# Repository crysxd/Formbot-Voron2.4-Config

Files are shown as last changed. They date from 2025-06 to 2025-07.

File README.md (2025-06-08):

# Formbot Voron 2.4 R2 Pro+

This is a basic config for the Formbot Voron 2.4 R2 Pro+ with instructions as a PDF file. I build the entire machine on stream:

https://www.youtube.com/watch?v=lysE0Ywv53w&list=PL1fjlNqlUKnUwgfOdnnUz_YEgj1KIZx8G&index=12

You can follow the streams and build along, but also keep an eye on the [PDF guide](https://github.com/crysxd/Voron2.4-Config/blob/main/Build%20Guide.pdf) as I e.g. later in the streams found out something could have been done better. It also goes into more detail on flashing the CB1, M8P and SB2209 and contains a list with things you need to print. You can also use my Orca Project files in the STL folder.

If you want to use my config, please compare your wiring to my [PDF guide](https://github.com/crysxd/Voron2.4-Config/blob/main/Build%20Guide.pdf).

If you plan to buy this kit please consider to use my affiliate link so I get a small kick back :) 
https://www.formbot3d.com/products/voron-24-r2-pro-corexy-3d-printer-kit-with-m8p-cb1-board-and-canbus-wiring-system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

The kit as I build it comes with:

- BTT CB1
- BTT M8P 2.0
- BTT SB2209 RP2040
- BTT HDMI5 screen

If a later revision of the kit uses different hardware please afjust accordingly

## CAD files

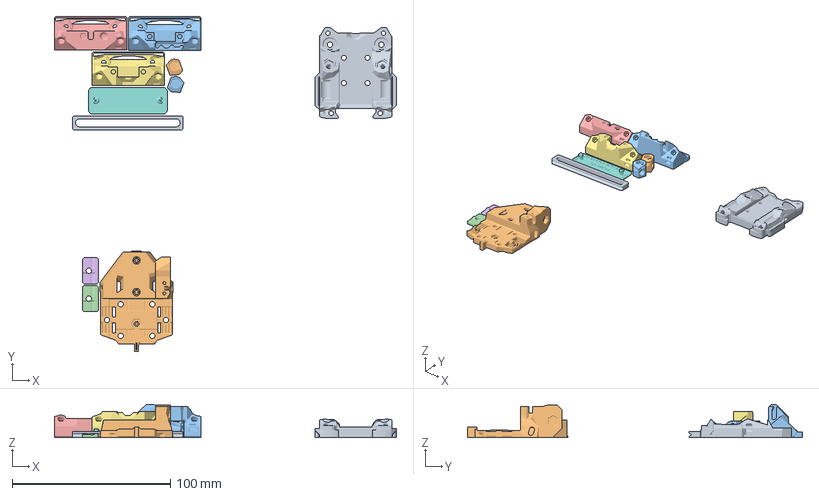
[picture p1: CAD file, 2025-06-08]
STLs/5) Tap.3mf
216.1 x 211.6 x 21.1 mm
Tap_Front_r8.stl
[a]_Tap_Center_r8.stl
Tap_Upper_Wired_r8.stl
[a]_Tap_Belt_Cover_r8_x2.stl x 2
Tap_Upper_D2HW_r8.stl
Tap_Upper_PCB_r8.stl
Printed_Cut_Guide.stl
MGN9_Assembly_Tool.stl
Tap_Center_right_r8.stl
Tap_Center_left_r8.stl

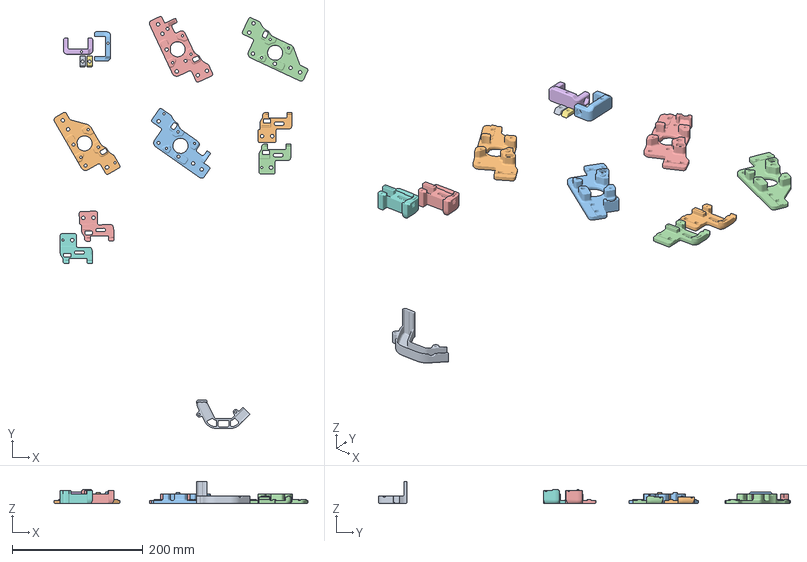
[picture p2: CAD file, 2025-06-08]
STLs/2) AB drives + idlers.3mf
388.8 x 631.0 x 34.0 mm
[a]_cable_cover.stl
front_idler_right_upper.stl
[a]_tensioner_right.stl
front_idler_left_lower.stl
front_idler_left_upper.stl
[a]_tensioner_left.stl
[a]_z_chain_retainer_bracket_x2.stl x 2
front_idler_right_lower.stl
b_drive_frame_lower.stl
a_drive_frame_lower.stl
b_drive_frame_upper.stl
a_drive_frame_upper.stl

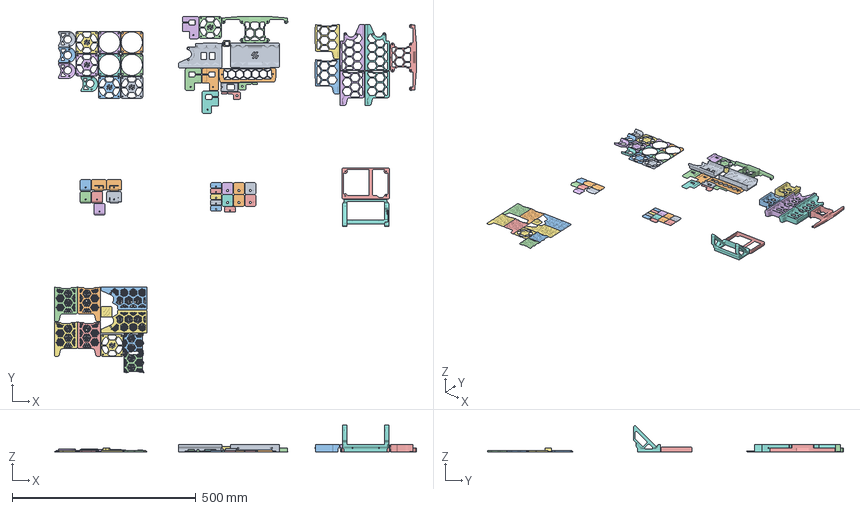
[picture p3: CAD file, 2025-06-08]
STLs/11) Skirts.3mf
983.8 x 968.4 x 72.4 mm
bottom_panel_maghold_panel_x6.stl x 6
[a]_fan_grill_retainer_x2.stl x 4
front-skirt-300-mesh-right.stl
BTT HDMI5 V1_2 mount frame_Regular.stl
front-skirt-300-mesh-left.stl
[a]_fan_grill_b_x2.stl x 3
side-skirt-300-mesh-left.stl
side_fan_support_x2.STL x 2
side-skirt-300-mesh-left(1).stl
[a]_fan_grill_a_x2.stl x 2
BTT HDMI5 V1_2 mount bracket_Regular.stl
[a]_belt_guard_b_x2.stl x 2
side-skirt-300-mesh-right.stl
[a]_belt_guard_a_x2.stl x 2
side-skirt-300-mesh-right(1).stl
rear_center_skirt_300.stl
side-skirt-center-mesh.stl x 2
rear-skirt-logo-insert.stl
keystone_panel.stl
exhaust_filter_grill.stl
bottom_panel_magclip_skirt_x6.stl x 6
[a]_exhaust_fan_grill.stl
z_belt_cover_b_x2.stl x 2
front_skirt_a_300.stl
z_belt_cover_a_x2.stl x 2
front_skirt_b_300.stl
side_skirt_a_300_x2.stl x 2
bowden_retainer.stl
bottom_panel_hinge_x2.stl x 3
[a]_exhaust_filter_mount_x2.stl x 2
side_skirt_b_300_x2.stl x 2
[a]_keystone_blank_insert.stl
bottom_panel_clip_x4.stl x 4

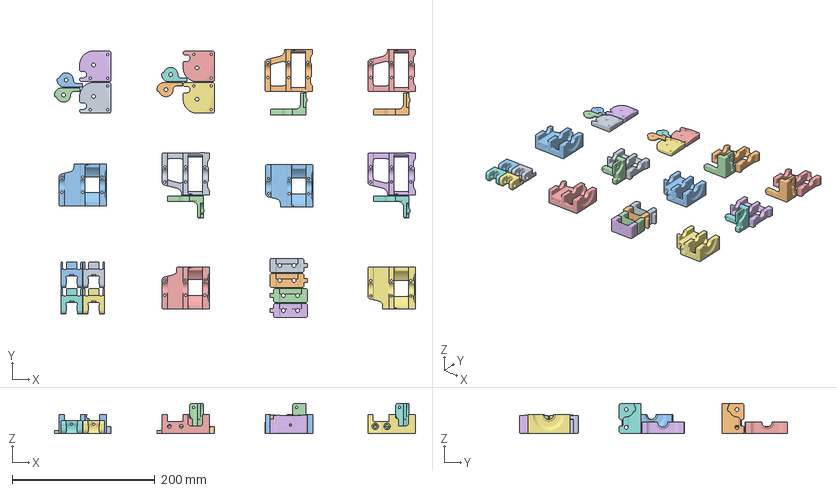
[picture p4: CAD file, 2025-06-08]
STLs/1) Z Drive.3mf
504.9 x 375.3 x 42.0 mm
z_tensioner_bracket_b_x2.stl x 2
z_drive_retainer_b_x2.stl x 2
z_drive_main_b_x2.stl x 2
z_motor_mount_b_x2.stl x 2
z_drive_main_a_x2.stl x 2
z_drive_retainer_a_x2.stl x 2
z_motor_mount_a_x2.stl x 2
[a]_z_tensioner_9mm_x4.stl x 4
z_tensioner_bracket_a_x2.stl x 2
[a]_z_drive_baseplate_a_x2.stl x 2
[a]_z_drive_baseplate_b_x2.stl x 2
[a]_belt_tensioner_b_x2.stl x 2
[a]_belt_tensioner_a_x2.stl x 2

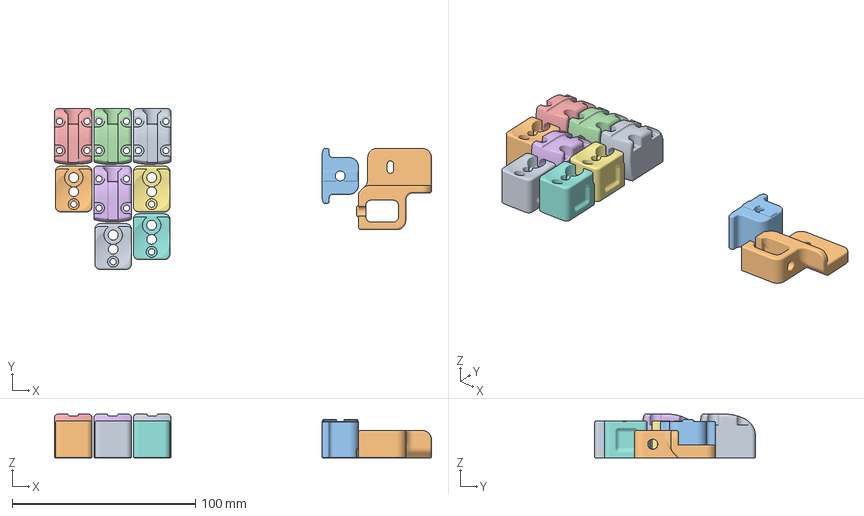
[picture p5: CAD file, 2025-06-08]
STLs/4) Z Axis.3mf
205.6 x 87.8 x 24.0 mm
z_joint_lower_x4.stl x 4
z_chain_bottom_anchor.stl
z_chain_guide.stl
z_joint_upper_x4.stl x 4

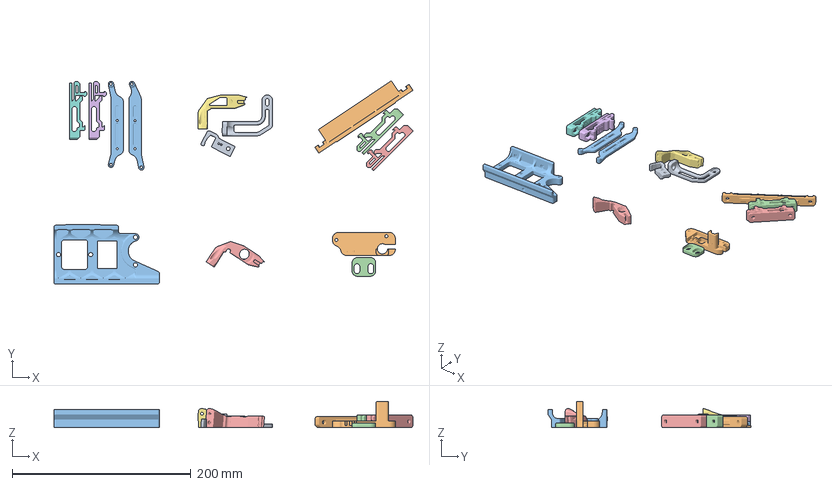
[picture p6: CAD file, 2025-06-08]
STLs/8) Electronics.3mf
402.0 x 227.7 x 29.3 mm
PSU_stabilizer_50mm.stl
Umbilical_cable_PG7_5mm_cable_cutout.stl
Manta_M8P_2pc.stl
Y bumper.stl
cw2-cable-bridge-pg7-can.stl
lrs_200_psu_bracket_x2.stl x 4
CW2 Cable_bridge.stl
Printed_Part_for_CAN_Cable_V1.2.stl
wago_221-415_mount_3by5.stl
power_inlet_filtered.stl

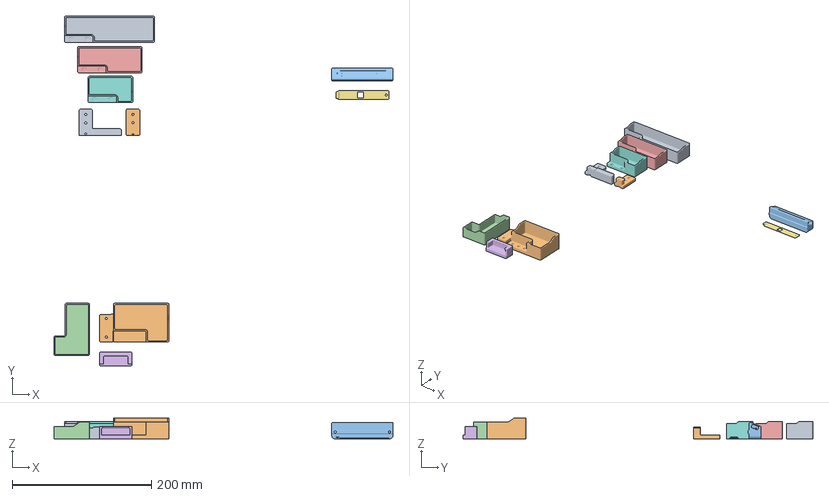
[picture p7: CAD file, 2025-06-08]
STLs/12) Addons.3mf
486.6 x 502.3 x 30.0 mm
0-SOLID-1
bucket-6x3-magnets.stl
happycam_main300.stl
bucket-insert.stl
0-SOLID-2
brush-holder-6x3-magnets.stl
cameradoor_120.stl
0-SOLID-3
0-SOLID-4
0-SOLID-5

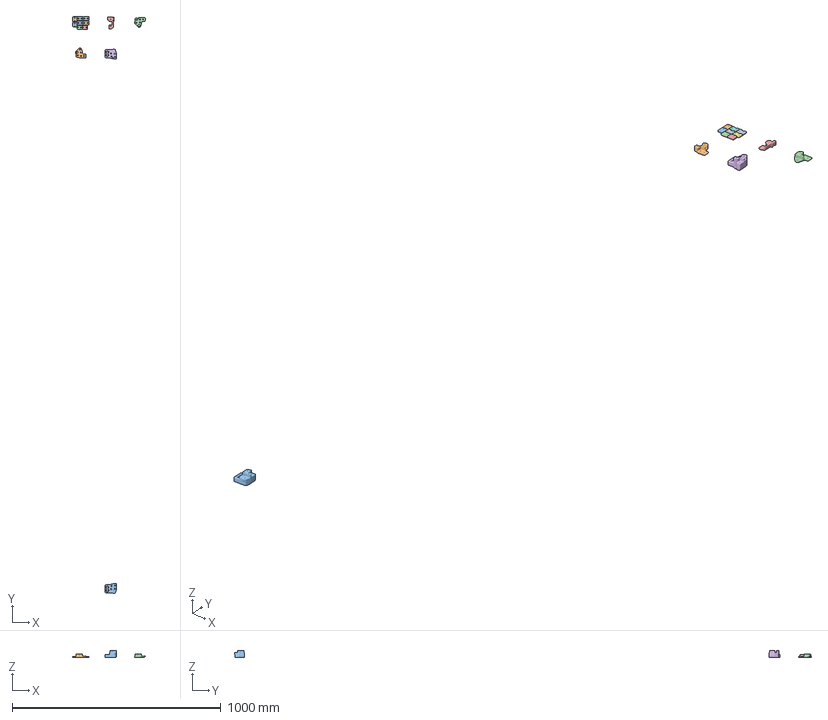
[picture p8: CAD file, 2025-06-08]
STLs/3) Gantry.3mf
348.0 x 2766.5 x 34.0 mm
[a]_z_belt_clip_upper_x4.stl x 4
xy_joint_left_upper_MGN12.stl
xy_joint_left_lower_MGN12.stl
xy_joint_right_upper_MGN12.stl
[a]_endstop_pod_D2F_switch.stl
xy_joint_right_lower_MGN12.stl
[a]_z_belt_clip_lower_x4.stl x 4

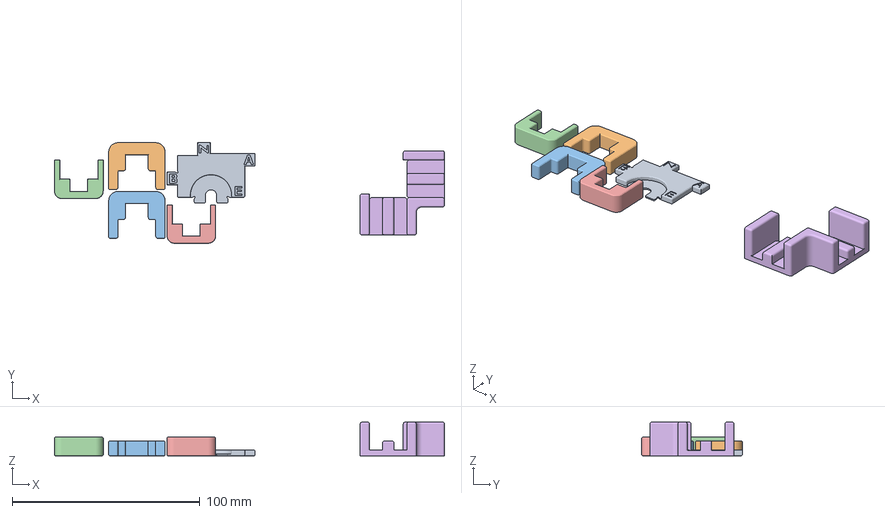
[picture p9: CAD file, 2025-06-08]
STLs/6) Tools.3mf
208.0 x 53.7 x 18.0 mm
pulley_jig.stl
MGN12_rail_guide_x2.stl x 2
MGN9_rail_guide_x2.stl x 2
jig.step

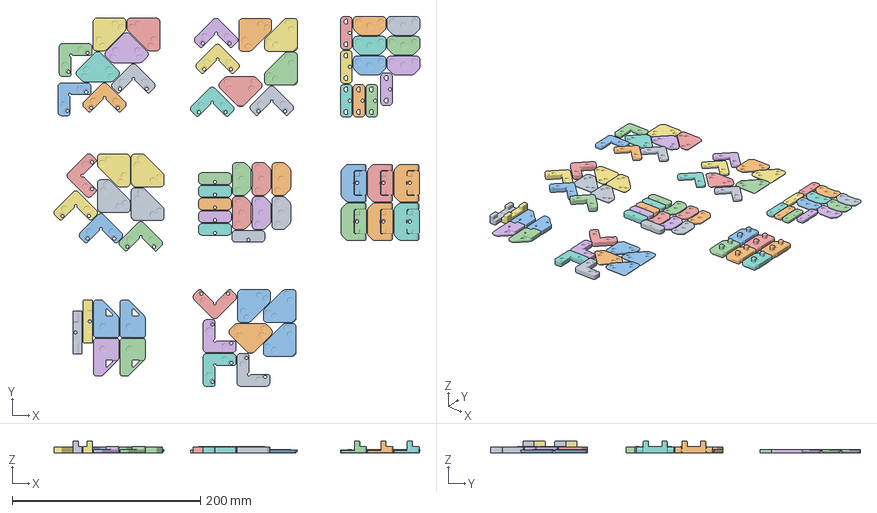
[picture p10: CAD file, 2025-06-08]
STLs/10) Panels.3mf
388.7 x 393.0 x 13.0 mm
magnetic_midspan_panel_clip_cap_3mm.stl x 12
magnetic_corner_panel_clip_cap.stl x 16
magnetic_midspan_panel_clip_base_3mm.stl x 6
midspan_6mm.stl x 6
corner_6mm.stl x 8
handle_a_x2.stl x 2
magnetic_corner_panel_clip_base_3mm.stl x 8
door_hinge_x6.stl x 6
handle_b_x2.stl x 2
latch_x2.stl x 2

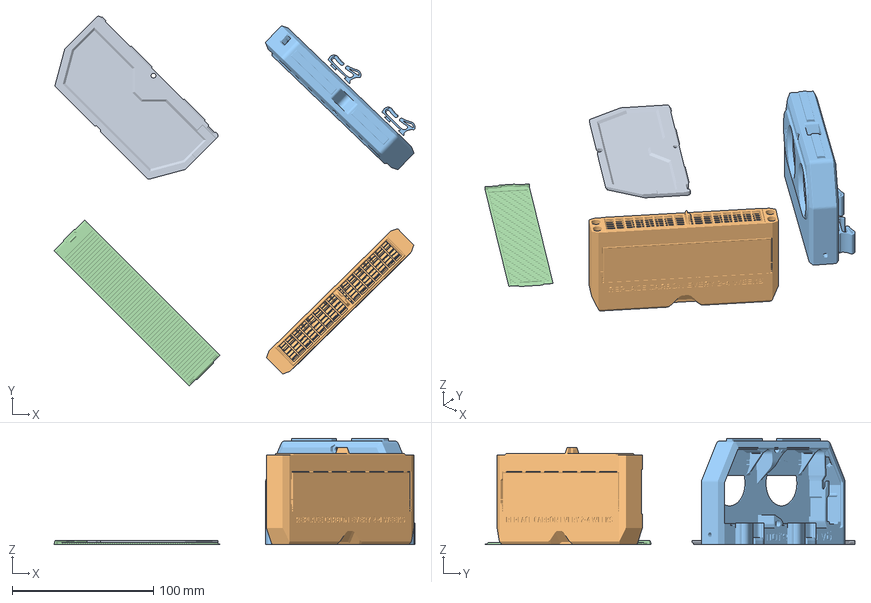
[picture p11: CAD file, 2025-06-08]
STLs/7) Nevermore.3mf
255.2 x 261.3 x 75.2 mm
V6_Plenum_Lid.stl
v6_Cartridge_90deg.stl
V6_Plenum[2020_extrusion].stl
[a]V6_Jalousie_Slicer.stl

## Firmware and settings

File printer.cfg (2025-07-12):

[include mainsail.cfg]
[include macros.cfg]





##########################################################################################################################################
##########################################################################################################################################
##########################################################################################################################################
# 	Basic config, need to check!
##########################################################################################################################################
##########################################################################################################################################
##########################################################################################################################################


# M8P 
[mcu]
canbus_uuid: f8bbc90dfa2d #CANBUS ID FOR M8P here replace with yours

# SB2209
[mcu ebb]
canbus_uuid: ef0499b67b66 #CANBUS ID FOR SB2209 here, replace with yours

[stepper_x]
# ADJUST 250 buid
# position_endstop: 250
# position_max: 250

# 300 build
position_endstop: 300
position_max: 300 

# ADJUST 350 buid
# position_endstop: 350
# position_max: 350

[stepper_y]
# ADJUST 250 buid
# position_endstop: 253
# position_max: 253

# 300 build
position_endstop: 303
position_max: 303 

# ADJUST 350 buid
# position_endstop: 353
# position_max: 353

[stepper_z]
# ADJUST 250 buid
# position_max: 240

# 300 build
position_max: 290

# ADJUST 350 buid
# position_max: 340

[extruder]
max_temp: 250 # ADJUST for Dragon hotend: 285

[quad_gantry_level]
# ADJUST: 250 build
# gantry_corners:
#	-60,-10
#	310, 320
# points:
#	25,25
#	25,200
#	225,200
#	225,25

# 300 build
gantry_corners:
	-60,-10
	360,370
points:
	25,25
	25,250
	275,250
	275,25

# ADJUST: 350 build
# gantry_corners:
# 	-60,-10
# 	410,420
# points:
# 	25,25
# 	25,300
# 	325,300
# 	325,25

[safe_z_home]
# ADJUST: 250 build
# home_xy_position: 125,125

# 300 build
home_xy_position: 150, 150

# ADJUST: 350 build
# home_xy_position: 175,175

[bed_mesh]
# ADJUST: 250 build
#mesh_max: 240,240

# 300 build
mesh_max: 290,290

# ADJUST: 350 build
#mesh_max: 340,340

[resonance_tester]
# ADJUST: 250 build
# probe_points: 125, 125, 20

# 300 build
probe_points: 150, 150, 20

# ADJUST: 350 build
# probe_points: 175, 175, 20



#####################################################################
# 	TMC autotune for silent and strong steppers
#####################################################################

# Uncomment below after installing the TMC autotune plugin
# This is optional but recommended
# https://github.com/andrewmcgr/klipper_tmc_autotune

# [autotune_tmc extruder]
# motor: moons-cse14hra1l410a
#
# [autotune_tmc stepper_x]
# motor: moons-ms17hd6p420I-05
#
# [autotune_tmc stepper_y]
# motor: moons-ms17hd6p420I-05
#
# [autotune_tmc stepper_z]
# motor: moons-ms17hd6p420I-05
#
# [autotune_tmc stepper_z1]
# motor: moons-ms17hd6p420I-05
#
# [autotune_tmc stepper_z2]
# motor: moons-ms17hd6p420I-05
#
# [autotune_tmc stepper_z3]
# motor: moons-ms17hd6p420I-05







##########################################################################################################################################
##########################################################################################################################################
##########################################################################################################################################
# 	Advanced config, not needed to edit for basic build
##########################################################################################################################################
##########################################################################################################################################
##########################################################################################################################################




#####################################################################
# 	MISC
#####################################################################


[printer]
kinematics: corexy
max_velocity: 700  
max_accel: 12000
max_z_velocity: 25
max_z_accel: 250
square_corner_velocity: 5.0

[idle_timeout]
timeout: 1800

[exclude_object]

[force_move] 
enable_force_move: true

[safe_z_home]
speed: 600
z_hop: 10

[bed_mesh]
speed: 350
horizontal_move_z: 2
mesh_min: 10,10
probe_count: 7,7
adaptive_margin: 5
mesh_pps: 2, 3
algorithm: bicubic
bicubic_tension: 0.2

[temperature_sensor MCU]
sensor_type: temperature_mcu

[temperature_sensor SoC]
sensor_type: temperature_host

[temperature_sensor EBB_NTC]
sensor_type: Generic 3950
sensor_pin: ebb:gpio28

[quad_gantry_level]
speed: 350
horizontal_move_z: 5
retries: 5
retry_tolerance: 0.0075
max_adjust: 10

[probe]
pin: ^ebb:gpio22
x_offset: 0
y_offset: 0
#z_offset: -1.900
lift_speed: 30
activate_gcode:
    {% set PROBE_TEMP = 150 %}
    {% set MAX_TEMP = PROBE_TEMP + 5 %}
    {% set ACTUAL_TEMP = printer.extruder.temperature %}
    {% set TARGET_TEMP = printer.extruder.target %}

    {% if TARGET_TEMP > PROBE_TEMP %}
        { action_respond_info('Extruder temperature target of %.1fC is too high, lowering to %.1fC' % (TARGET_TEMP, PROBE_TEMP)) }
        M109 S{ PROBE_TEMP }
    {% else %}
        # Temperature target is already low enough, but nozzle may still be too hot.
        {% if ACTUAL_TEMP > MAX_TEMP %}
            { action_respond_info('Extruder temperature %.1fC is still too high, waiting until below %.1fC' % (ACTUAL_TEMP, MAX_TEMP)) }
            TEMPERATURE_WAIT SENSOR=extruder MAXIMUM={ MAX_TEMP }
        {% endif %}
    {% endif %}

#####################################################################
# 	X/Y Stepper Settings
#####################################################################

## X Stepper on Motor1(B Motor)
[stepper_x]
step_pin: PG9
dir_pin: PD7
enable_pin: !PG11
microsteps: 16
rotation_distance: 40
full_steps_per_rotation:200  
endstop_pin: ^ebb:gpio24
position_min: 0
homing_speed: 100                 
homing_retract_dist: 5
homing_positive_dir: true

[tmc2209 stepper_x]
uart_pin: PG10
interpolate: True
run_current: 0.8
sense_resistor: 0.110
stealthchop_threshold: 0

[stepper_y]
step_pin: PG13
dir_pin: PG12
enable_pin: !PG15
microsteps: 16
rotation_distance: 40
endstop_pin: ^PF3
full_steps_per_rotation:200 
position_min: 0
homing_speed: 100
homing_retract_dist: 5
homing_positive_dir: true

[tmc2209 stepper_y]
uart_pin: PG14
interpolate: True
run_current: 0.8
sense_resistor: 0.110
stealthchop_threshold: 0


#####################################################################
# 	Z Stepper Settings
#####################################################################

## Z0 Stepper - Check wiring diagaram in PDF guide on GitHub!
[stepper_z]
step_pin: PE6
dir_pin: PE5
enable_pin: !PC14
rotation_distance: 40
gear_ratio: 80:16
microsteps: 16
endstop_pin: probe:z_virtual_endstop
position_min: -10
homing_speed: 8
second_homing_speed: 3
homing_retract_dist: 3

[tmc2209 stepper_z]
uart_pin: PC13
interpolate: true
run_current: 0.8
sense_resistor: 0.110
stealthchop_threshold: 1

##	Z1 Stepper - Check wiring diagaram in PDF guide on GitHub!
[stepper_z1]
step_pin: PE2
dir_pin: !PE1
enable_pin: !PE4
rotation_distance: 40
gear_ratio: 80:16
microsteps: 16

[tmc2209 stepper_z1]
uart_pin: PE3
interpolate: true
run_current: 0.8
sense_resistor: 0.110
stealthchop_threshold: 1

##	Z2 Stepper - Check wiring diagaram in PDF guide on GitHub!
[stepper_z2]
step_pin: PB8
dir_pin: PB7
enable_pin: !PE0
rotation_distance: 40
gear_ratio: 80:16
microsteps: 16

[tmc2209 stepper_z2]
uart_pin: PB9
interpolate: true
run_current: 0.8
sense_resistor: 0.110
stealthchop_threshold: 1

##	Z3 Stepper - Check wiring diagaram in PDF guide on GitHub!
[stepper_z3]
step_pin: PB4
dir_pin: !PB3
enable_pin: !PB6
rotation_distance: 40
gear_ratio: 80:16
microsteps: 16

[tmc2209 stepper_z3]
uart_pin: PB5
interpolate: true
run_current: 0.8
sense_resistor: 0.110
stealthchop_threshold: 1


#####################################################################
# 	Bed Heater
#####################################################################

[heater_bed]
heater_pin: PA1
sensor_type: Generic 3950
sensor_pin: PB1
max_power: 1.0
min_temp: 0
max_temp: 120
control: pid
pid_kp: 58.437
pid_ki: 2.347
pid_kd: 363.769


#####################################################################
# 	Fan Control
#####################################################################

[fan_generic nevermore]
##	Print Cooling Fan - CNC_FAN0
pin: PF8
kick_start_time: 0.5
##	Depending on your fan, you may need to increase this value
##	if your fan will not start. Can change cycle_time (increase)
##	if your fan is not able to slow down effectively
off_below: 0.10
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

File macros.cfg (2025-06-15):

[delayed_gcode after_startup_1]
initial_duration: 1.
gcode:
  LIGHT_PENDING
  
[delayed_gcode after_startup_2]
initial_duration: 5.
gcode:
  LIGHT_OFF

[gcode_macro G32]
gcode:
    BED_MESH_CLEAR
    G28
    QUAD_GANTRY_LEVEL
    G28

[gcode_macro FILTER_ON]
gcode:
    SET_FAN_SPEED FAN=nevermore SPEED=0.8

[gcode_macro FILTER_OFF]
gcode:
    SET_FAN_SPEED FAN=nevermore SPEED=0
   
[gcode_macro PRINT_START]
gcode:
    {% set BED_TEMP = params.BED_TEMP|default(60)|float %}
    {% set EXTRUDER_TEMP = params.EXTRUDER_TEMP|default(190)|float %}
    {% set BRUSH_NOZZLE = params.BRUSH_NOZZLE|default(0)|float %}
    LIGHT_PENDING
  	# Start TLM Start G-Code
	# Clear Display
	M117
	# Clear Existing Feedrate
	M220 S100
	# Clear Existing Flowrate
	M221 S100
    # Heat bed
    M140 S{BED_TEMP}
    # Brush nozzle if enabled by param
    {% if BRUSH_NOZZLE > 0 %}
	    G28
        NOZZLE_PRIME_AND_BRUSH EXTRUDER_TEMP={EXTRUDER_TEMP}
    {% endif %}
    G32
    # Wait for Bed
    M190 S{BED_TEMP}
    BED_MESH_CALIBRATE ADAPTIVE=1
	# Move to side and wait for final temps
    M109 S{EXTRUDER_TEMP}
    G1 X1 Y10 Z5 F3000
    G91
    G1 E25 F3600
    
	# Relative Extruder
	M83
	# Set units to millimeters
	G21 
	# Use absolute coordinates
	G90
	# Use absolute distances for extrusion
	M82
	# Fan Off
	M107
    {% if BED_TEMP > 90 %}
      FILTER_ON
    {% endif %}
    
	NOZZLE_PURGE
    LIGHT_PRINTING
    
   

[gcode_macro PRINT_END]
#   Use PRINT_END for the slicer ending script - please customise for your slicer of choice
gcode:
    SAVE_GCODE_STATE NAME=STATE_PRINT_END

    M400                           ; wait for buffer to clear
    G92 E0                         ; zero the extruder
    G1 E-25.0 F3600                ; retract filament

    G91                            ; relative positioning
    G0 Z1.00 X20.0 Y20.0 F20000    ; move nozzle to remove stringing
    TURN_OFF_HEATERS
    M107                           ; turn off fan
    G1 Z2 F3000                    ; move nozzle up 2mm
    G90                            ; absolute positioning
    G0  X125 Y250 F3600            ; park nozzle at rear
    BED_MESH_CLEAR

    GET_POSITION
    
    # The purpose of the SAVE_GCODE_STATE/RESTORE_GCODE_STATE
    # command pair is to restore the printer's coordinate system
    # and speed settings since the commands above change them.
    # However, to prevent any accidental, unintentional toolhead
    # moves when restoring the state, explicitly set MOVE=0.
    RESTORE_GCODE_STATE NAME=STATE_PRINT_END MOVE=0
    LIGHT_OFF
    FILTER_OFF

[gcode_macro LIGHT_PENDING]
gcode:
  SET_LED LED=toolhead_light RED=1 GREEN=0.02 BLUE=0.02 WHITE=0 INDEX=1 TRANSMIT=0
  SET_LED LED=toolhead_light RED=0 GREEN=0 BLUE=0 WHITE=0 INDEX=2 TRANSMIT=0
  SET_LED LED=toolhead_light RED=0 GREEN=0 BLUE=0 WHITE=0 INDEX=3 TRANSMIT=1
  SET_PIN PIN=caselight VALUE=0

[gcode_macro LIGHT_PRINTING]
gcode:
  SET_LED LED=toolhead_light RED=0 GREEN=0.0 BLUE=0.0 WHITE=0.5
  SET_PIN PIN=caselight VALUE=0.8

[gcode_macro LIGHT_OFF]
gcode:
  SET_LED LED=toolhead_light RED=0 GREEN=0.02 BLUE=0 WHITE=0 INDEX=1 TRANSMIT=0
  SET_LED LED=toolhead_light RED=0 GREEN=0 BLUE=0 WHITE=0 INDEX=2 TRANSMIT=0
  SET_LED LED=toolhead_light RED=0 GREEN=0 BLUE=0 WHITE=0 INDEX=3 TRANSMIT=1
  SET_PIN PIN=caselight VALUE=0

[gcode_macro NOZZLE_PRIME_AND_BRUSH]
gcode:
   {% set EXTRUDER_TEMP = params.EXTRUDER_TEMP|default(190)|float %}

  # Move over bucker
  G0 X298 Y303 Z10 F9000

  # Purge
  M104 S{EXTRUDER_TEMP}
  TEMPERATURE_WAIT sensor=extruder MINIMUM={EXTRUDER_TEMP-5} MAXIMUM={EXTRUDER_TEMP+5}
  M83  
  G1 E50 F500
  G1 E-5  F500
  M104 S150

  # Brush
  {% for i in range(10) %}
    G0 X238 Y299 F5000
    G0 X278 Y302 F5000
  {% endfor %}

  G0 Y290 F3000

[gcode_macro NOZZLE_PURGE]
description: Draw a purge line at the front left edge of the build plate
gcode:
  CHOME
  G0 X2.5 Y2 F6000 ; Go to front
  G0 Z0.2 ; Drop to bed
  M83 ; Set extruder to relative mode
  G1 X25 E10 F500 ; Extrude 25mm of filament in a 4cm line
  G1 X50 F5000 ; Quickly wipe away from the filament line
  G1 X75 E2.00 F1500
  G1 E-0.1 F400 ; Retract a little
  G1 Z0.5 ; Raise and begin printing.

[gcode_macro CHOME]
description: Homes XYZ axis only if printer is in a non-homed state
gcode:
  {% if "xyz" not in printer.toolhead.homed_axes or printer["quad_gantry_level"].applied == false %}
    G32
  {% endif %}

[gcode_macro TEST_SPEED]
# Home, get position, throw around toolhead, home again.
# If MCU stepper positions (first line in GET_POSITION) are greater than a full step different (your number of microsteps), then skipping occured.
# We only measure to a full step to accomodate for endstop variance.
# Example: TEST_SPEED SPEED=300 ACCEL=5000 ITERATIONS=10

description: Test for max speed and acceleration parameters for the printer. Procedure: Home -> ReadPositionFromMCU -> MovesToolhead@Vel&Accel -> Home -> ReadPositionfromMCU

gcode:
    # Speed
    {% set speed  = params.SPEED|default(printer.configfile.settings.printer.max_velocity)|int %}
    # Iterations
    {% set iterations = params.ITERATIONS|default(5)|int %}
    # Acceleration
    {% set accel  = params.ACCEL|default(printer.configfile.settings.printer.max_accel)|int %}
    # Minimum Cruise Ratio
    {% set min_cruise_ratio = params.MIN_CRUISE_RATIO|default(0.5)|float %}
    # Bounding inset for large pattern (helps prevent slamming the toolhead into the sides after small skips, and helps to account for machines with imperfectly set dimensions)
    {% set bound = params.BOUND|default(20)|int %}
    # Size for small pattern box
    {% set smallpatternsize = SMALLPATTERNSIZE|default(20)|int %}
    
    # Large pattern
        # Max positions, inset by BOUND
        {% set x_min = printer.toolhead.axis_minimum.x %}
        {% if x_min < 0 %}
            {% set x_min = 0 %}
        {% endif %}
    
        {% set y_min = printer.toolhead.axis_minimum.y %}
        {% if y_min < 0 %}
            {% set y_min = 0 %}
        {% endif %}
    
        {% set x_min = x_min + bound %}
        {% set x_max = printer.toolhead.axis_maximum.x - bound %}
        {% set y_min = y_min + bound %}
        {% set y_max = printer.toolhead.axis_maximum.y - bound %}
    
    # Small pattern at center
        # Find X/Y center point
        {% set x_center = (printer.toolhead.axis_minimum.x|float + printer.toolhead.axis_maximum.x|float ) / 2 %}
        {% set y_center = (printer.toolhead.axis_minimum.y|float + printer.toolhead.axis_maximum.y|float ) / 2 %}
        
        # Set small pattern box around center point
        {% set x_center_min = x_center - (smallpatternsize/2) %}
        {% set x_center_max = x_center + (smallpatternsize/2) %}
        {% set y_center_min = y_center - (smallpatternsize/2) %}
        {% set y_center_max = y_center + (smallpatternsize/2) %}

    # Save current gcode state (absolute/relative, etc)
    SAVE_GCODE_STATE NAME=TEST_SPEED
    
    # Output parameters to g-code terminal
    { action_respond_info("TEST_SPEED: starting %d iterations at speed %d, accel %d" % (iterations, speed, accel)) }
    
    # Home and get position for comparison later:
        M400 # Finish moves - https://github.com/AndrewEllis93/Print-Tuning-Guide/issues/66
        G28
        # QGL if not already QGLd (only if QGL section exists in config)
        {% if printer.configfile.settings.quad_gantry_level %}
            {% if printer.quad_gantry_level.applied == False %}
                QUAD_GANTRY_LEVEL
                G28 Z
            {% endif %}
        {% endif %} 
        # Move 50mm away from max position and home again (to help with hall effect endstop accuracy - https://github.com/AndrewEllis93/Print-Tuning-Guide/issues/24)
        G90
        G1 X{printer.toolhead.axis_maximum.x-50} Y{printer.toolhead.axis_maximum.y-50} F{30*60}
        M400 # Finish moves - https://github.com/AndrewEllis93/Print-Tuning-Guide/issues/66
        G28 X Y
        G0 X{printer.toolhead.axis_maximum.x-1} Y{printer.toolhead.axis_maximum.y-1} F{30*60}
        G4 P1000 
        GET_POSITION

    # Go to starting position
    G0 X{x_min} Y{y_min} Z{bound + 10} F{speed*60}

    # Set new limits
    {% if printer.configfile.settings.printer.minimum_cruise_ratio is defined %}
        SET_VELOCITY_LIMIT VELOCITY={speed} ACCEL={accel} MINIMUM_CRUISE_RATIO={min_cruise_ratio}
    {% else %}
        SET_VELOCITY_LIMIT VELOCITY={speed} ACCEL={accel} ACCEL_TO_DECEL={accel / 2}
    {% endif %}
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

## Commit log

2025-05-20 Udpate config
    [macros.cfg, printer-board-cb1.cfg, printer-board-ebb.cfg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]
2025-06-08 Add README and files
    [1) Z Drive.3mf, 10) Panels.3mf, 11) Skirts.3mf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]
2025-06-08 Update for dragon
    [printer.cfg]
2025-06-08 Remove unused files
    [mainsail.cfg, timelapse.cfg]
2025-06-08 Add missing 350 config
    [printer.cfg]
2025-06-15 Reduce default max temp
    [printer.cfg]
2025-06-15 Move to single file
    [printer-board-ebb.cfg, printer-board-m8p.cfg, printer-extras.cfg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]
2025-06-15 Fix Y endstop
    [printer.cfg]
2025-06-15 Unlink old files
    [printer.cfg]
2025-06-15 Update guide
    [printer.cfg]
2025-06-15 Small changes
    [printer.cfg]
2025-06-15 Remove autosave
    [printer.cfg]
2025-06-15 Disable nozzle brush by default
    [macros.cfg]
2025-07-12 Move rear QGL positions forward to prevent collision with brush while probing
    [printer.cfg]
